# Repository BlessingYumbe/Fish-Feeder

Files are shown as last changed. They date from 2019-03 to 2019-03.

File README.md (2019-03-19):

# Fish-Feeder
Set up a hydroponic garden / fish tank installation using a hardware and the internet of things to automate monitoring or maintaining of the system.

# Problem Statement:
For our team project, the group was tasked to set up a hydroponic garden / fish tank installation using hardware and the internet of things to automate monitoring or maintaining of the system.  We have decided to automate feeding of the fish to allow remote feeding when access to the tank installation is not available.   Using Python, the group has interacted with an Arduino to remotely initialize dispensing fish food into the tank and output the status back to a ThingSpeak channel whether or not the feeding was successful.  Additionally, our Feeder apparatus will use a photocell to determine if food remains available for the feed to continue to dispense.  If the photocell detects that the feeder is empty, the system reports that status to ThingSpeak and the dispense food requests is alerted to the status.

## Hardware Setup
### Bill of Materials

|component|vendor|
|---|---|
|Arduino|[SparkFun RedBoard - Programmed with Arduino](https://www.sparkfun.com/products/13975)|
|Breadboard|[Connect Circuit	Breadboard - Self-Adhesive](https://www.sparkfun.com/products/12002)|
|Base|[Hold Boards	Arduino and Breadboard Holder](https://www.sparkfun.com/products/11235)|
|USB Cable|[Connect to Computer	SparkFun USB Mini-B Cable - 6 Foot](https://www.sparkfun.com/products/11301)|
|Jumper Wires|[Circuit Connections	Jumper Wires Standard 7" M/M - 30 AWG (30 Pack)](https://www.sparkfun.com/products/11026)|
|Stepper|[Motor	Drive Feeder	Stepper Motor with Cable](https://www.sparkfun.com/products/938)|
|Motor Driver|[Control Motor	EasyDriver - Stepper Motor Driver](https://www.sparkfun.com/products/12779)|
|Photocell	Light|[Sensor	Mini Photocell](https://www.sparkfun.com/products/9088)|
|Green LED|[Ready Indicator	LED - Basic Green 5mm](https://www.sparkfun.com/products/9592)|
|Yellow LED|[	Run Indicator	LED - Basic Yellow 5mm	](https://www.sparkfun.com/products/9594)|
|Red LED|[Error Indicator	LED - Basic Red 5mm	](https://www.sparkfun.com/products/9590)|
|3 x 330 Ω Resistor|[	Limit Current	Resistor 330 Ω 1/6th Watt PTH](https://www.sparkfun.com/products/8377)|
|1 x 10k Ω Resistor|[	Divide Voltage	Resistor 10k Ω 1/6th Watt PTH](https://www.sparkfun.com/products/8374)|

## Cad prototypes
Here are the cad prototypes designed for the project

The [Body1.stl](Body1.stl) AUTOCAD

The [Body2.stl](Body2.stl) AUTOCAD

The [Body3.stl](Body3.stl) AUTOCAD

The [Body8.stl](Body8.stl) AUTOCAD

The [Body9.stl](Body9.stl) AUTOCAD

The [Body16.stl](Body16.stl) AUTOCAD

## Cad Prototypes after being printed
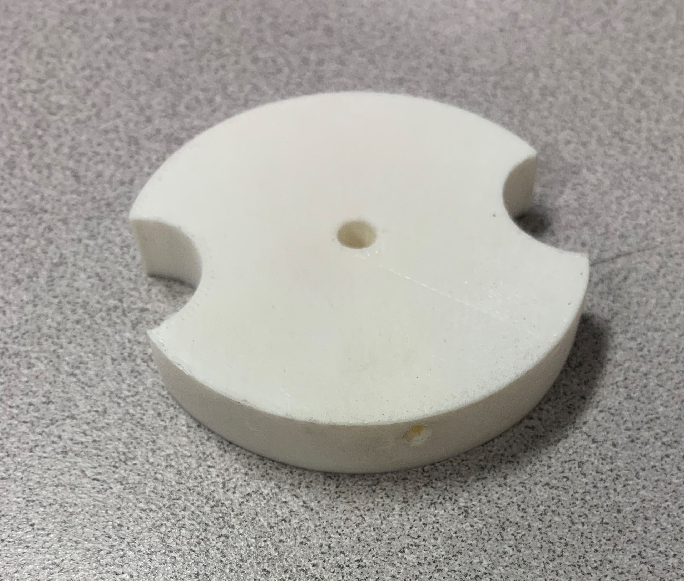
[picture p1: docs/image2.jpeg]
docs

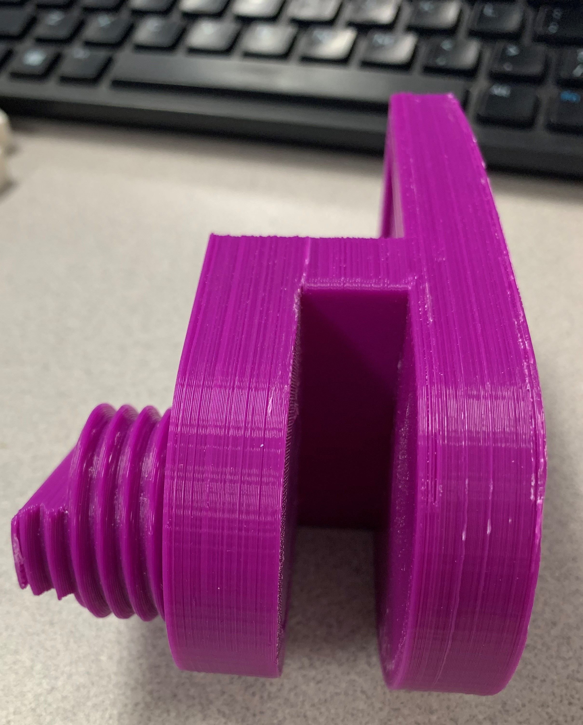
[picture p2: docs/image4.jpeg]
docs

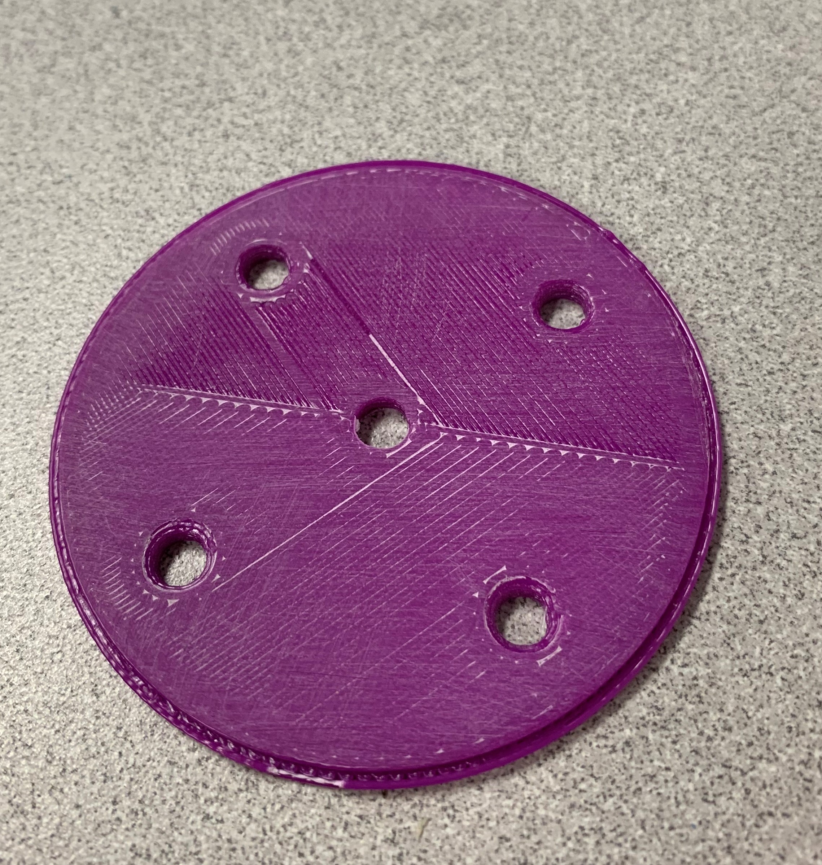
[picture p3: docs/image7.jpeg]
docs


### Fritzing Diagram
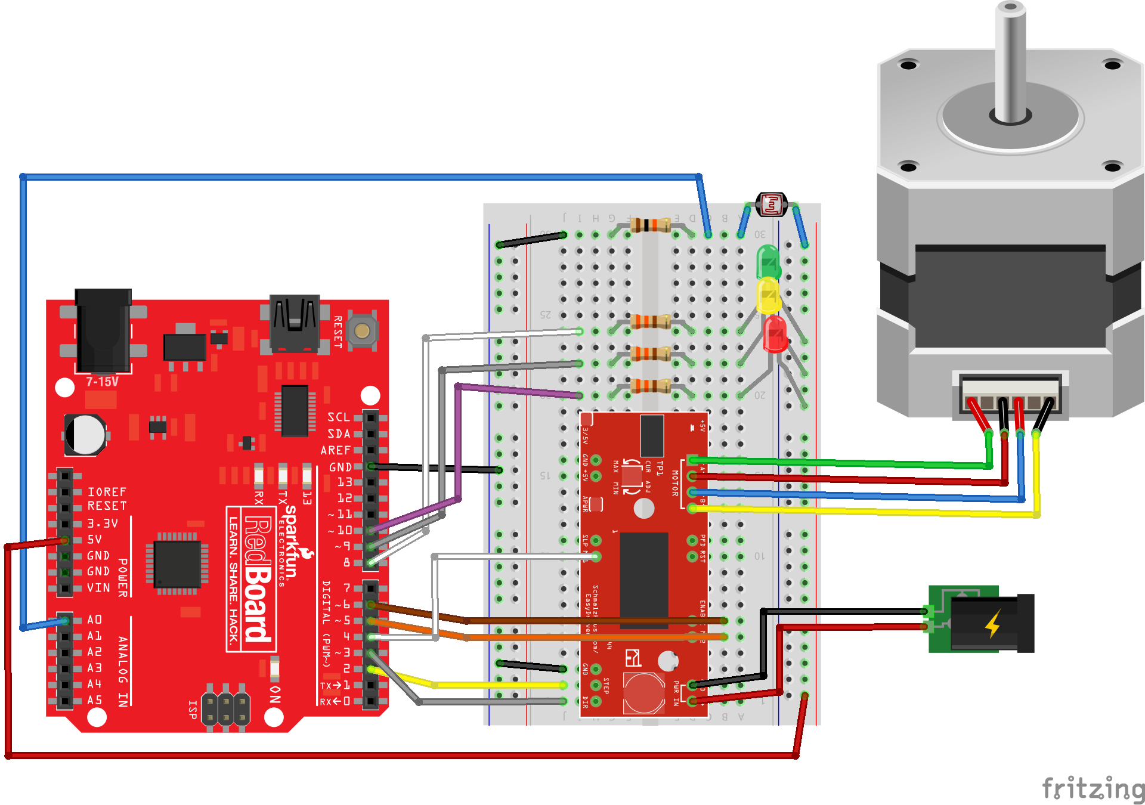
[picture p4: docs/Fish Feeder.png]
docs


## Connected Hardware

Arduino is connected to the computer via a mini-USB 

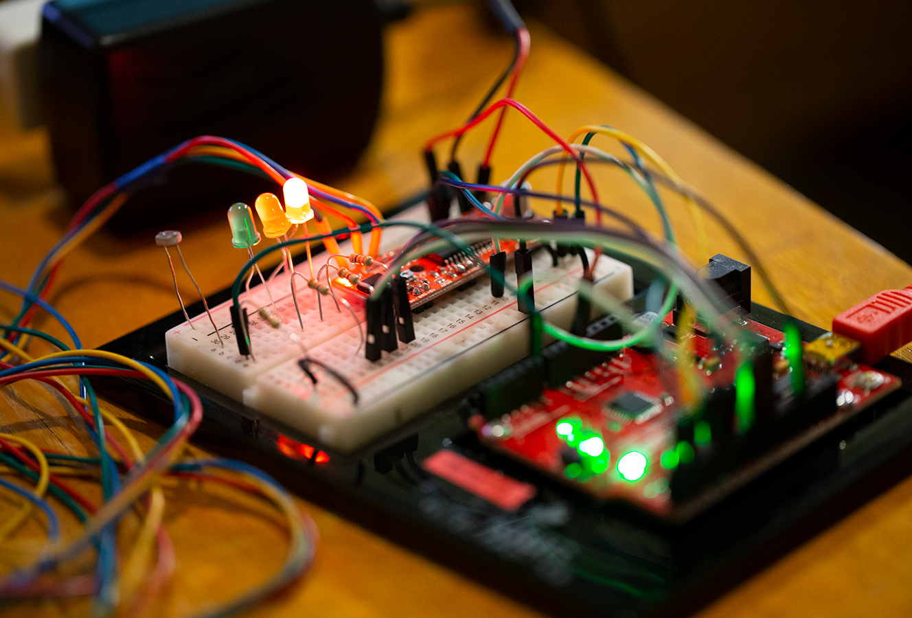
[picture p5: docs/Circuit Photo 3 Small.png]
docs


## Arduino Code
The [fish_feeder.ino](fish_feeder.ino) sketch was uploaded on the Arduino using the Arduino IDE.

## Python Code

The [fish_feerder.py](fish_feerder.py) script was run in python.

## Results

Screenshot from ThingSpeak Channel showing resulting status updates when fish are fed.

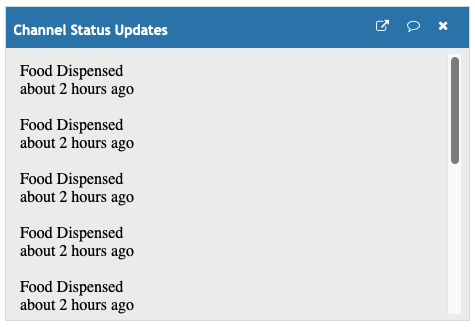
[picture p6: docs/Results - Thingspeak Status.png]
docs


## Future Work
This project was quite interesting to set up with the hydroponic fish garden. While using Python, the program was taking time initialize the code itself to prevent multiple ThingSpeak write requests in too short of a time. For future work, another group improve the communication scheme to reduce this delay and prevent failed requests to dispense food.  Additionally, another group could add hardware that can monitor and control conditions such as temperature, lighting, water flow/waste inside the fish garden. And all of these could be fully automated and controlled remotely using a smartphone.

## License
The MIT License Copyright <2019><Team Fish Food>

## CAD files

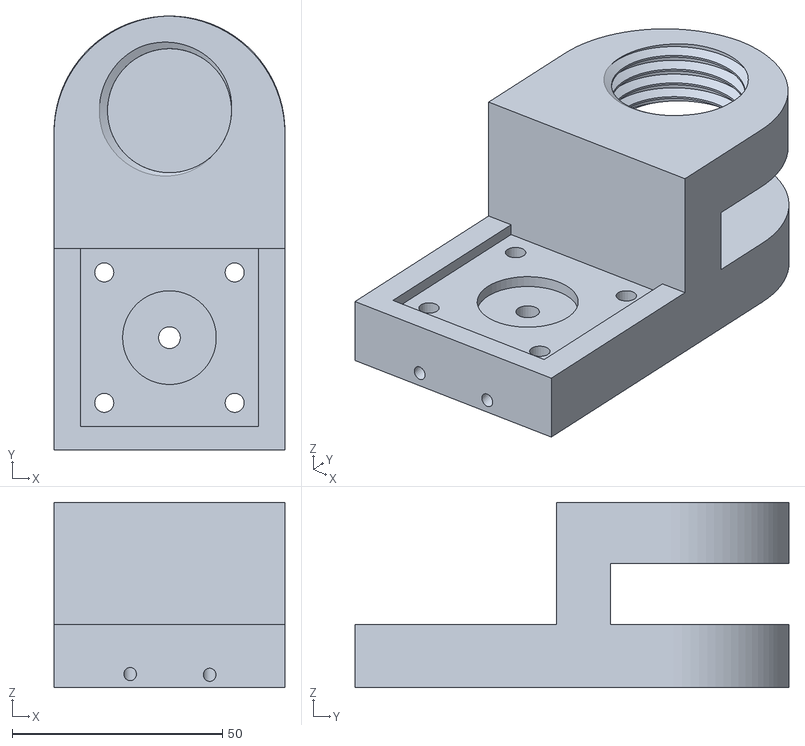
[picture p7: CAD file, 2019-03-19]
Body8.stl
54.9 x 103.2 x 44.0

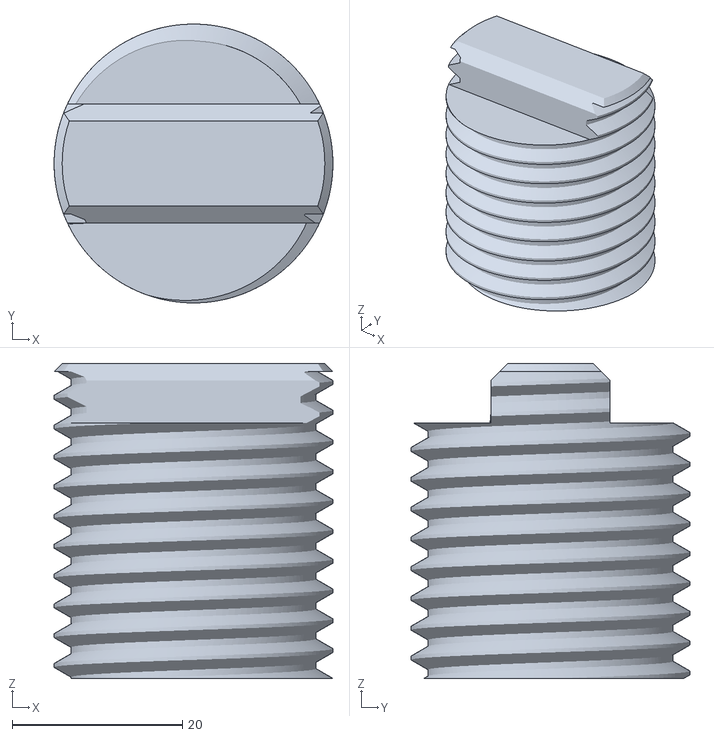
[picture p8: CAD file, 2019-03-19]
Body9.stl
32.8 x 32.8 x 37.0

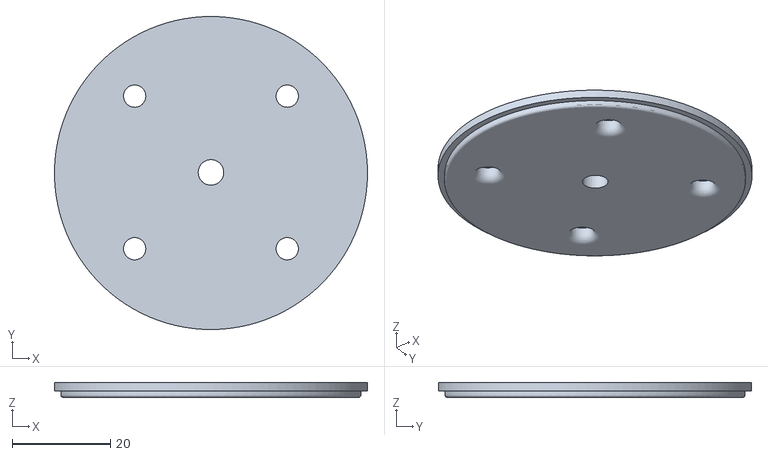
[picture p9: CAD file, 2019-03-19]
Body3.stl
63.6 x 63.6 x 3.00

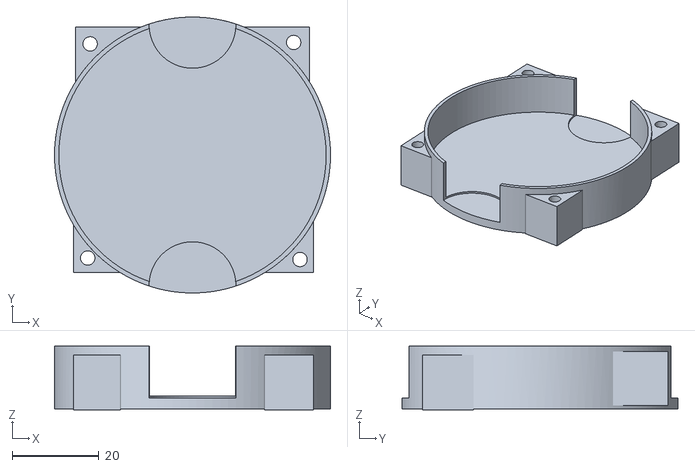
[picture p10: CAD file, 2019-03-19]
Body2.stl
63.6 x 63.6 x 14.7

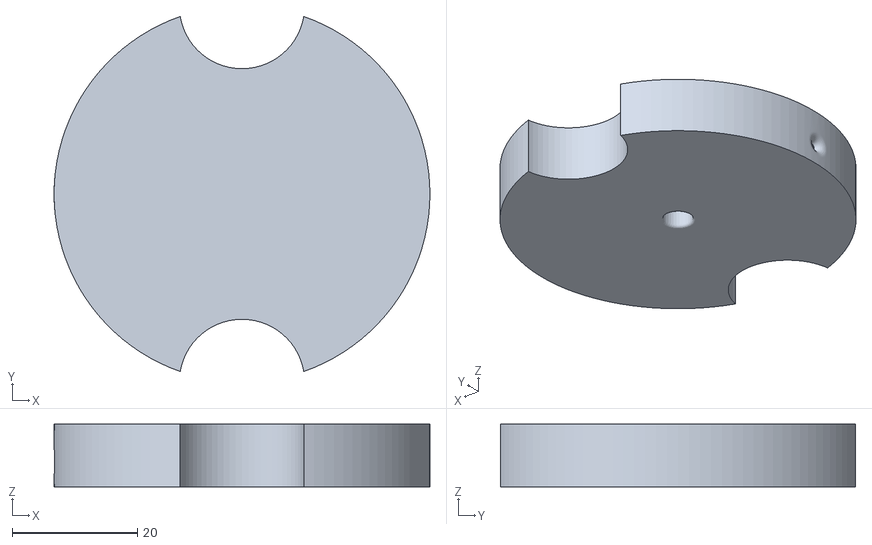
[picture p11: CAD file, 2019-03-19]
Body1.stl
60.0 x 56.7 x 10.0

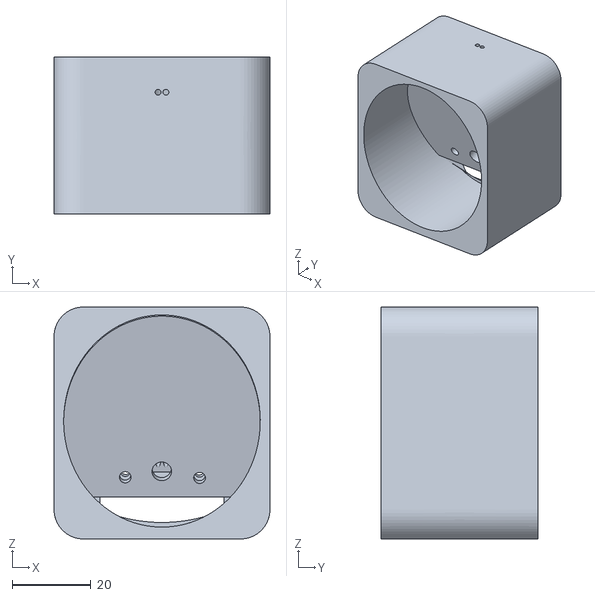
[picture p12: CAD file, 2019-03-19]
Body16.stl
54.9 x 40.0 x 59.0

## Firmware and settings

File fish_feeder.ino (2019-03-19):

/*
 * Fish_Feeder.ino
 * Team Fish Food Group Project
 * ENGR 114 - Winter 2019
 * Arduino Code by Jon Golobay
 * Last Edited: 3/11/19
 */

//Declare I/O
#define stp 2
#define dir 3
#define MS1 4
#define MS2 5
#define EN 6
#define green 8
#define yellow 9
#define red 10

//declare and initialize variables
int user_input = 0;
int photoresistor = 0;  
int threshold = 150;  //photoresistor threshold, determined experimentally and may depend on lighting conditions

void setup() {
  //intialize hardware setup with intial states
  Serial.begin(9600); 
  pinMode(green, OUTPUT);
  pinMode(yellow, OUTPUT);
  pinMode(red, OUTPUT);
  pinMode(stp, OUTPUT);
  pinMode(dir, OUTPUT);
  pinMode(MS1, OUTPUT);
  pinMode(MS2, OUTPUT);
  pinMode(EN, OUTPUT);
  //LEDs are active LOW, write to HIGH to initialize to off
  digitalWrite(red, HIGH);
  digitalWrite(green, HIGH);
  digitalWrite(yellow, HIGH);
  //initialize step motor
  resetMotor();
}

void loop() {
  //delay to slow down serial output
  delay(500);
  //read analog value of voltage change due to photresistor
  photoresistor = analogRead(A0);
  if(photoresistor>threshold) {
    //LED Switch: Red ON and Green/Yellow OFF
    digitalWrite(red, LOW);
    digitalWrite(green, HIGH);
    digitalWrite(yellow, HIGH);
    //output status to serial
    Serial.println("EMPTY");
    //always read serial input to ensure feed requests while feeder is empty are read and disregarded
    //failure to do so will store requests until feeder is ready and run as many times as requested
    while(Serial.available()) {
      user_input = Serial.read();
    }
  }
  
  if(photoresistor<threshold) {   
    //LED Switch: Green ON and Red/Yellow OFF
    digitalWrite(green, LOW);
    digitalWrite(yellow, HIGH);
    digitalWrite(red, HIGH);
    //output status to serial
    Serial.println("READY");
    
    //reads serial input looking for dispense trigger which is byte='1'
    while(Serial.available()) {
      user_input = Serial.read();
      if (user_input =='1') {    
        //LED Switch: Yellow ON and Green OFF
        digitalWrite(green, HIGH);
        digitalWrite(yellow, LOW);
        //Step Motor Enable
        digitalWrite(EN, LOW); 
        //output status to serial
        Serial.println("DISPENSING");
        //loop to run step motor for 800 steps(step number determined experimentally and dependent on dispense mechanism)
        for(int x= 1; x<800; x++) {
          digitalWrite(stp,HIGH); //Trigger one step
          delay(1);
          digitalWrite(stp,LOW); //Pull step pin low so it can be triggered again
          delay(1);
        }
        //output status to serial
        Serial.println("COMPLETE");
        //LED Switch: Yellow ON and Green OFF
        digitalWrite(yellow, HIGH);
        digitalWrite(green, LOW);
        //Step Motor Disable
        digitalWrite(EN, HIGH);
      }
    }      
  }
}

//function to initialze step motor to a default state
void resetMotor() {
  digitalWrite(stp, LOW);
  digitalWrite(dir, LOW); //direction pin LOW to go "forward"
  digitalWrite(MS1, HIGH);
  digitalWrite(MS2, HIGH);
  digitalWrite(EN, HIGH); //enable pin HIGH for disable
}
  

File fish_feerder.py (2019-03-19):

#imports needed
import time
import serial
import urllib
import pandas as pd
import numpy as np

#function to read and return value of single thingspeak field
def read_field_thingspeak(channel, api_key, field, results):
    read_link = 'https://api.thingspeak.com/channels/' + str(channel) + '/fields/' + str(field) + '.csv?api_key=' + str(api_key) +'&results=' + str(results)
    df = pd.read_csv(urllib.request.urlopen(read_link))
    df.drop(['created_at'], axis=1, inplace=True)
    return np.array(df)[0][1]

#function that reads thingspeak status
def read_status_thingspeak(channel, api_key, results):
    read_link = 'https://api.thingspeak.com/channels/' + str(channel) + '/status.csv?api_key=' + str(api_key) +'&results=' + str(results)
    return urllib.request.urlopen(read_link)

#function that formats and requests a link to write to two thingspeak fields at once
def write_to_thingspeak(api_key, field1, value1, field2, value2):
    write_link = 'https://api.thingspeak.com/update?api_key=' + str(api_key) + '&field'+ str(field1) +'=' + str(value1) +'&field'+ str(field2) +'=' + str(value2)
    urllib.request.urlopen(write_link)

#function to write status to thingspeak in addtion to both fields
def write_to_thingspeak_status(api_key, field1, value1, field2, value2, status):
    write_link = 'https://api.thingspeak.com/update?api_key=' + str(api_key) + '&field'+ str(field1) +'=' + str(value1) +'&field'+ str(field2) +'=' + str(value2) +'&status=' + status
    urllib.request.urlopen(write_link)

#declare variables related for specific thingspeak channel    
channel = '720608'
read_api_key = 'RRGPJE5YQ8JJPRIR'
write_api_key='C7MKD36DWMJS69UL'

#declare variable for COM port for serial communication
com = '/dev/cu.usbserial-DN051CFK'

#declare variables to validate user input
function_selection = ''
action = ''
print('Fish Feeder Transceiver')
while(function_selection != '0'):
    print('***Main Menu***')
    #prompt user to choose between transmitter or receiver functionality
    function_selection = input('Choose the following:\n1: Transmitter\n2: Receiver\n0: Exit\n')
    if function_selection == '1':
        #while loop that runs for duration of program to prompt for user input
        while(action != '0'):
            #initialization delay to prevent multiple thingspeak write attempts within a short period.
            print('\nInitializing', end='')
            for i in range(15):
                print('.', end='')
                time.sleep(1)
            #prompt user for input and move through program accordingly
            action = input('\n\n***Transmitter***\nChoose the following:\n1: Feed Fish!\n2: Last Time Fish Fed?\n3: Feeder Status\n0: Exit\n')               
            if action == '1':
                #read initial feeder status
                status = read_field_thingspeak(channel,read_api_key,1,1)
                if(status != 0):
                    #if status not empty write the run command to thingspeak
                    write_to_thingspeak(write_api_key,1,1,2,1)
                    #communication delay to ensure time for arduino to process command and respond to thingspeak
                    print('Communicating', end='')
                    for i in range(20):
                        print('.', end='')
                        time.sleep(1)
                
                    #read feeder status to check if feeding was succesful    
                    status = read_field_thingspeak(channel,read_api_key,1,1)
                    if(status==0):
                        print('\nFeeder Empty!')
                        continue
                    elif(status == 1):
                        #read feeder command, if command is still 1 then hardware never read command, if 0 then hardware ran command
                        command = read_field_thingspeak(channel,read_api_key,2,1)
                        if(command == 1):
                            print('\nFeeder Not Responding!')
                        else: 
                            print('\nFood Dispensed.')
                else:
                    #if status is 0 then the feeder is empty
                    print('\nFeeder Empty!')
            elif action == '2':
                #query time last fed and report to user
                df = pd.read_csv(read_status_thingspeak(channel, read_api_key, 1))
                print('Fish last fed', np.array(df)[0][0])
                continue
            elif action == '3':
                #query feeder status and report to user
                #field 1:status(0=EMPTY, 1=READY)
                #field 2:command(0=IDLE, 1=RUN)
                status = read_field_thingspeak(channel,read_api_key,1,1)
                command = read_field_thingspeak(channel,read_api_key,2,1)
                if(status==0):
                    print('Feeder Empty!')
                elif(status==1):
                    print('Feeder Ready.')     
            elif action == '0':
                #terminate program
                print("Transmitter Terminated.")
                break
            else:
                print('Invalid Input!\n\n')
                continue
                
                
    elif function_selection == '2':
        print('***Receiver***')
        try:
            #initialize serial communication
            ser = serial.Serial(com, 9600, timeout=1)
            time.sleep(2)
        except:
            print('Serial Communication Error!\nReturning to Main Menu.\n\n')
        else:
            #while loop that runs while serial communication is open
            while ser.is_open:
    
                #query thingspeak for feeder status and command
                #field 1:status(0=EMPTY, 1=READY)
                #field 2:command(0=IDLE, 1=RUN)
                status = read_field_thingspeak(channel,read_api_key,1,1)
                command = read_field_thingspeak(channel,read_api_key,2,1)
    
                #reset input buffer to ensure latest serial output from board is read
                ser.reset_input_buffer()
                board_status = ser.readline()
    
                #board is communicating empty status
                if(board_status == b'EMPTY\r\n'):
                    if(status!=0):
                        write_to_thingspeak(write_api_key,1,0,2,0)
                        time.sleep(15)
            
                #board is commmunicating ready status
                if(board_status == b'READY\r\n'):
                    #command is IDLE
                    if(command == 0):
                        if(status != 1):
                            write_to_thingspeak(write_api_key,1,1,2,0)
                            time.sleep(15)
                    #command is RUN
                    if(command == 1):
                        ser.write(b'1')
                        time.sleep(15)
                        write_to_thingspeak_status(write_api_key,1,1,2,0,'Food Dispensed')
                #delay    
                time.sleep(1)
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
